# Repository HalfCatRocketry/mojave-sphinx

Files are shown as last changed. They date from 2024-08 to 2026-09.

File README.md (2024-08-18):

Mojave Sphinx is a high-power amateur rocket with a liquid bipropellant propulsion system powered by nitrous oxide and any number of solvent or hydrocarbon fuels. It is designed to be as simple and economical as possible so that an individual or team with high-power or experimental rocketry experience can build and launch it within a reasonable timeline and budget. Half Cat Rocketry provides the following:
- Build, Integration and Launch Guidebook - HCR-5100 (PDF)
- SolidWorks CAD files (.sldprt)
- SolidWorks drawing files (.slddrw)
- Drawing package (PDF)
- 3D models of machined, printed, and flat-cut components (.step and .stl)
- Vector files of flat-cut components (.dxf)
- HalfCatSim v1.3.8 motor simulation (.xlsx)
- Sample thrust curve file (.eng)
- OpenRocket simulation file (.ork)

Please note that the SolidWorks CAD was created in the version 2022 student edition and is for educational purposes.

Half Cat Rocketry is not liable for the usage of this content, and the authors bear no responsibility for the usage of its content. Read the following disclaimer before continuing.

DISCLAIMER:

By viewing, downloading, printing, or otherwise possessing the content in this repository you agree to the terms and conditions of its use, which are provided below. If you do not agree to the terms and conditions, you are required to remove this content from your possession by deleting all digital copies and/or disposing of printed materials in an environmentally responsible manner. Failure to do so shall constitute a violation of the license under which this content is distributed.

This content is provided as is, with absolutely NO WARRANTY, express or implied, including no warranty of merchantability or fitness for any particular purpose. You (“the user”) agree by your continued viewing or possession of this content to hold harmless and release from all liability the authors and any associated parties for any outcome resulting from your use or misuse of this material. The authors bear no responsibility for the usage of the this content, and any and all liability for injury, property damage, financial loss, death, or other harm arising from its use or misuse rests solely with the user.

This content is provided solely for informational and entertainment purposes and does not constitute an endorsement of, nor a recommendation to engage in, any particular activity, method, or practice. The information contained in this content solely represents the personal experiences of the authors and does not promise, guarantee, or predict any specific outcome of any particular activity, method, or practice.

The user acknowledges by continued viewing or possession of this content that rocketry and all associated activities, including but not limited to the procurement, manufacture, assembly, disassembly, modification, storage, handling, transport, operation, testing, launching, recovery and disposal of rocket and rocket motor systems, components, propellants, and accessories are inherently dangerous and may pose a direct and immediate hazard to health, life, and property.

Mentions of any particular products within this content by part number, name, description, brand, chemical formula, or any other identifier DO NOT constitute an endorsement of said products, nor is any warranty of merchantability or fitness for any particular purpose of said products expressed or implied by the authors of this content. Should the user purchase any product mentioned, listed, or otherwise discussed in this content, the user is solely responsible for determining the suitability of any and all products for the user’s specific application. The user is solely responsible for any outcome or liability arising from the use or misuse of any products named, described, or otherwise alluded to in this content.

As stated above, your (“the user’s”) continued viewing or possession of the content in this repository constitutes acknowledgement of and agreement to these warnings, terms, and conditions. If you do not agree to these terms and conditions, or do not wish to acknowledge the warnings provided herein, you are required to remove this content from your possession by deleting all digital copies and/or disposing of printed materials in an environmentally responsible manner. Failure to do so shall constitute a violation of the license under which this content is distributed.

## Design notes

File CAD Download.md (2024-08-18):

[Mojave Sphinx CAD Download](//drive.google.com/uc?export=download&id=1ExKPyPkNKFJ8Lf6YcyjYc9QDEeFzdeIZ) (Google Drive download link)

Please note that the zip file is large. (~250 MB)

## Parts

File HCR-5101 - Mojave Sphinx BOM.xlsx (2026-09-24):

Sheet: Cover Page
HCR-5101 | Mojave Sphinx Bill of Materials
Revision | 01 | This Bill of Materials (BOM) is a companion document to HCR-5100, the Mojave Sphinx Build, Integration, and Launch Guidebook. It is intended to be an easier format for referencing the book's BOM and purchasing parts. This document, HCR-5101, is considered the source of truth for the guidebook's BOM. It is separately controlled and released, allowing Half Cat Rocketry to make corrections or updates as necessary without needing to generate a revision of HCR-5100. A note on Revision 01: To avoid confusion between the guidebook's BOM (which does not reference this separate document, as it did not exist at the time of publication) and the BOM presented here, all descriptions and prices have been left as-shown in HCR-5100 R01, with only minor corrections to fix typos or broken links. More comprehensive updates will be introduced in the next revision, which will coincide with the release of HCR-5100 R02. A note on Amazon links: Amazon is a large marketplace with many stores and listings that often change much faster than we can keep up with. Therefore, Amazon line items generically link to the main website rather than a specific item's page. It is intended for the purchaser to search using the provided vendor description and part number then select appropriate items.
Release Date | 2026-04-25
Associated With | HCR-5100 (R01)
Revision | Release Date
01 | 2026-04-25

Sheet: Mojave Sphinx
A1 | Propellant Tank
Line | Item | Unit Price | QTY | Cost | Context | PN | Vendor Description | Source | Line | Alternate Source #1 | Alternate Source #2
1 | 6061 Aluminum Round 4"D X 1/2"L | $14.95 | 2 | $29.90 | Tank Bulkheads | 1610T37-1610T134 | Multipurpose 6061 Aluminum 4" Diameter (1/2 in) | https://www.mcmaster.com/1610T37-1610T134/ | 1
2 | 6061 Aluminum Round 4"D X 3"L | $22.26 | 1 | $22.26 | Tank Piston | 1610T37-1610T33 | Multipurpose 6061 Aluminum 4" Diameter (3 in) | https://www.mcmaster.com/1610T37-1610T33/ | 2
3 | 6061 Aluminum Tube 4"D X 1/8"W X 36"L | $85.38 | 1 | $85.38 | Tank Casing | 9056K42-9056K423 | Multipurpose 6061 Aluminum Round Tube 1/8" Wall Thickness, 4" OD (3 ft) | https://www.mcmaster.com/9056K42-9056K423/ | 3
4 | 6061 Aluminum Tube 4"OD X 1/2"W X 3"L | $10.37 | 2 | $20.74 | Bolted Tank Rings | 7392T17-7392T173 | Multipurpose 6061 Aluminum Round Tube 1/4" Wall Thickness, 4" OD (3 in) | https://www.mcmaster.com/7392T17-7392T173/ | 4
5 | -238 Buna-N O-Rings (Pack of 50) | $16.14 | 1 | $16.14 | Tank/Piston Seals | 9452K226 | Oil-Resistant Buna-N O-Ring 1/8 Fractional Width, Dash Number 238 | https://www.mcmaster.com/9452K226/ | 5
6 | 5/16-24 X 1/2" Button Head Screw (Pack of 25) | $7.57 | 1 | $7.57 | Tank Bolts | 91255A378 | Button Head Hex Drive Screw Black-Oxide Alloy Steel, 5/16"-24 Thread, 1/2" Long | https://www.mcmaster.com/91255A378/ | 6
7 | 5/16-24 Offset Narrow Base Weld Nut (Pack of 25) | $9.21 | 1 | $9.21 | Tank Bolt Nuts | 94579A550 | Steel Offset-Barrel Narrow-Base Weld Nut 5/16"-24 Thread Size | https://www.mcmaster.com/94579A550/ | 7
8 | 1/4-20 X 7/8 Button Head Hex Drive Screws (Pack of 50) | $9.30 | 1 | $9.30 | Fwd Bulkhead Recovery Anchors, Fin Brackets, Airframe | 91306A279 | Button Head Hex Drive Screws Zinc-Plated Alloy Steel, 1/4"-20 Thread, 7/8" Long | https://www.mcmaster.com/91306A279/ | 8
9 | 1/4-20 Coupling Nut | $0.39 | 2 | $0.78 | Fwd Bulkhead Recovery Anchors | 90264A435 | Zinc-Plated Steel Coupling Nut Low-Strength, 1/4"-20 Thread Size | https://www.mcmaster.com/90264A435/ | 9
10 | Sealing Washers for 1/4" Screw, 0.5" OD (Pack of 10) | $7.49 | 1 | $7.49 | Fwd Bulkhead Recovery Anchors | 91367A952 | Chemical-Resistant Fluorosilicone Sealing Washer for 1/4" Screw Size,.230" ID,.5" OD,.052" to .072" Thick | https://www.mcmaster.com/91367A952/ | 10
11 | Ultra-Low-Profile Socket Head Screw Alloy Steel, 1/4"-20 Thread Size, 1/2" Long | $4.93 | 2 | $9.86 | Propellant Piston Extraction | 90357A013 | Ultra-Low-Profile Socket Head Screw Alloy Steel, 1/4"-20 Thread Size, 1/2" Long | https://www.mcmaster.com/90357A013/ | 11
12 | Spacer, for 5/16”, 5/8” OD x 1/2" Long | $4.31 | 1 | $4.31 | Bushing for Tank Drill Jig | 93320A215 | Polished Unthreaded Spacers 5/8" OD, 1/2" Long, for 5/16" Screw Size | https://www.mcmaster.com/93320A215/ | 12
13 | Propellant Tank Casing | $0.00 | 1 | $0.00 | Machined | TANK-36L-047V2X8X313C | - | Made from 9056K423 | 13
14 | Fuel Tank Bulkhead | $0.00 | 1 | $0.00 | Machined | BKHD-FL-O238-4NPT2X250C | - | Made from 1610T134 | 14
15 | Oxidizer Tank Bulkhead | $0.00 | 1 | $0.00 | Machined | BKHD-OX-O238–8NPT4NPT | - | Made from 1610T134 | 15
16 | Propellant Piston | $0.00 | 1 | $0.00 | Machined | PSTN-2XO238-250T20 | - | Made from 1610T33 | 16
17 | Interface Ring | $0.00 | 2 | $0.00 | Machined | INRG-200S-8X3125C8X250C | - | Made from 7392T173 | 17
18 | Nut Retaining Ring | $0.00 | 2 | $0.00 | Printed | NTRG-45C20D-200E | - | Made from printer filament | 18
19 | Propellant Tank Drill Jig | $0.00 | 1 | $0.00 | Printed | DRLJG-TANK-8X625OD-BSHNG | - | Made from printer filament | 19
 |  | Subtotal |  | $222.94
A2 | Fluid System
Line | Item | Unit Price | QTY | Cost | Context | PN | Vendor Description | Source | Line | Alternate Source #1 | Alternate Source #2
1 | Aluminum Pipe Nipple, 1/4NPT, 4"L | $5.09 | 2 | $10.18 | Tank outlets to valves | 44665K137 | Standard-Wall Aluminum Pipe Nipple Threaded on Both Ends, 1/4 NPT, 4" Long | https://www.mcmaster.com/44665K137/ | 1
2 | Brass High Pressure Elbow Fitting, M/F, 1/4NPT | $2.94 | 2 | $5.88 | Fuel valve outlet | 50785K43 | High-Pressure Brass Pipe Fitting 90 Degree Elbow Adapter, 1/4 NPT Female x Male | https://www.mcmaster.com/50785K43/ | 2
3 | High-Pressure Brass Straight Reducer, 1/4 x 1/8 NPT Male | $2.64 | 1 | $2.64 | Fuel valve outlet | 5485K31 | High-Pressure Brass Pipe Fitting Straight Reducer, 1/4 x 1/8 NPT Male | https://www.mcmaster.com/5485K31/ | 3
4 | High-Pressure Brass Elbow Connector, 1/8 NPT Female | $3.31 | 1 | $3.31 | Fuel valve outlet | 50785K35 | High-Pressure Brass Pipe Fitting 90 Degree Elbow Connector, 1/8 NPT Female | https://www.mcmaster.com/50785K35/ | 4
5 | 37 Degree Flared Adapter for 5/16" Tube OD, 1/8 Pipe Size | $5.38 | 1 | $5.38 | Fuel valve outlet | 50675K435 | 37 Degree Flared Fitting for Copper Tubing Straight Adapter for 5/16" Tube OD, 1/8 Pipe Size | https://www.mcmaster.com/50675K435/ | 5
6 | High-Pressure Braided Chemical Hose with Fittings Brass 1/2"-20 Thread Size Flare UNF Female, 3/8" OD - 42" | $30.36 | 1 | $30.36 | Fuel Line 42" Section | 4468K858 | High-Pressure Braided Chemical Hose with Fittings Brass 1/2"-20 Thread Size Flare UNF Female, 3/8" OD (42 in) | https://www.mcmaster.com/4468K812-4468K858/ | 6
7 | High-Pressure Braided Chemical Hose with Fittings Brass 1/2"-20 Thread Size Flare UNF Female, 3/8" OD - 14" | $19.32 | 1 | $19.32 | Fuel Line 14" Section | 4468K031 | High-Pressure Braided Chemical Hose with Fittings Brass 1/2"-20 Thread Size Flare UNF Female, 3/8" OD (14 in) | https://www.mcmaster.com/4468K812-4468K031/ | 7
8 | High-Pressure Braided Chemical Hose with Fittings Brass 9/16"-18 Thread Size Flare UNF Female, 7/16" OD – 12” | $27.61 | 1 | $27.61 | Ox Line | 4468K865 | High-Pressure Braided Chemical Hose with Fittings Brass 9/16"-18 Thread Size Flare UNF Female, 7/16" OD (12 in) | https://www.mcmaster.com/4468K813-4468K865/ | 8
9 | 37 Degree Flared Straight Connector for 5/16" Tube OD, 1-3/8" Long | $4.47 | 1 | $4.47 | Fuel Line Union | 50675K135 | 37 Degree Flared Fitting for Copper Tubing Straight Connector for 5/16" Tube OD, 1-3/8" Long | https://www.mcmaster.com/50675K135/ | 9
10 | 37 Degree Flared Adapter for 3/8" Tube OD x 1/4 NPT Male | $3.65 | 1 | $3.65 | Ox Valve Outlet | 50675K163 | 37 Degree Flared Fitting for Copper Tubing Adapter for 3/8" Tube OD x 1/4 NPT Male | https://www.mcmaster.com/50675K163/ | 10
11 | Nylon Tubing, 1/4" OD, 800PSI, 10ft | $11.50 | 1 | $11.50 | Fill tube | 9685T3 | High-Pressure Hard Plastic Tubing for Air&Water Nylon, Semi-Clear White, 0.15" ID, 1/4" OD (10 ft) | https://www.mcmaster.com/9685T3/ | 11
12 | Check Valve, 1/8NPT Female/Male, Brass | $15.00 | 1 | $15.00 | Fill | 7768K21 | Brass Threaded Check Valve with Brass Piston, 1/8 NPT Female x NPT Male | https://www.mcmaster.com/7768K21/ | 12
13 | Elbow, 1/8NPT, Male/Female, Brass | $2.16 | 1 | $2.16 | Fill check to QD | 50785K41 | High-Pressure Brass Pipe Fitting 90 Degree Elbow Adapter, 1/8 NPT Female x Male | https://www.mcmaster.com/50785K41/ | 13
14 | Push to Connect Fitting, 1/4" Tube X 1/8NPT | $3.95 | 2 | $7.90 | Fill check to QD | 9396T31 | High-Pressure Push-to-Connect Tube Fitting for Air and Water, Adapter, 1/4" Tube OD x 1/8 NPTF Male | https://www.mcmaster.com/9396T31/ | 14
15 | 3/4" X 6" 6061-T6 Round Bar | $4.39 | 1 | $4.39 | QD Stock Material | 8974K299 | Multipurpose 6061 Aluminum 3/4" Diameter (1/2 ft) | https://www.mcmaster.com/8974K11-8974K299/ | 15
16 | -007 Buna-N O-rings (Pack of 100) | $4.25 | 1 | $4.25 | QD Seal | 9452K15 | Oil-Resistant Buna-N O-Ring 1/16 Fractional Width, Dash Number 007 | https://www.mcmaster.com/9452K15/ | 16
17 | High Pressure Brass Straight adapter, 1/4NPT Female x Male | $2.66 | 1 | $2.66 | Fuel valve outler spacer | 50785K27 | High-Pressure Brass Pipe Fitting Straight Adapter with Hex Body, 1/4 NPT Female x Male | https://www.mcmaster.com/50785K27/ | 17
18 | Quick Disconnect, ¾” x ⅛” Flange, 9/32” Female Bore, 1/8 NPT | $0.00 | 1 | $0.00 | Machined | QDC-750X125FLG-281FB8NPT |  | Made from 8974K299 | 18
19 | Quick Disconnect, ¾” x ⅛” Flange, .270 Male Barb, -007 O-Ring Gland | $0.00 | 1 | $0.00 | Machined | QDC-750x125FLG-270MB-O007 |  | Made from 8974K299 | 19
20 | Quick Disconnect Clip, for ¾” x ⅛” Flange | $0.00 | 1 | $0.00 | Printed | QDC-750X250CLP |  | Made from printer filament | 20
 |  | Subtotal |  | $160.66
A3 | Valves
Line | Item | Unit Price | QTY | Cost | Context | PN | Vendor Description | Source | Line | Alternate Source #1 | Alternate Source #2
1 | M3x0.5 10mm Low Profile Socket Head Screw, 18-8SS (Pack of 25) | $2.28 | 1 | $2.28 | Servo Horn Connector | DS3225 | 2Pack 25KG High Torque RC Servo Waterproof servo Compatible with 1/6, 1/8, 1/10, 1/12 RC Car, Full Metal Gear Steering Servo with 25T Servo Horn (270°) | https://www.amazon.com/ | 1
2 | 25kg Servo w/ 25T Servo Horn (Pack of 2) | $28.99 | 1 | $28.99 | Fuel/Ox valve actuators | 4112T22 | Compact High-Pressure Brass Ball Valve 2 | https://www.mcmaster.com/4112T22/ | 2
3 | Compact High Pressure Ball Valve, 1/4NPT | $17.26 | 2 | $34.52 | Fuel/Ox Valves | 90480A009 | Low-Strength Steel Hex Nut 1 | https://www.mcmaster.com/90480A009/ | 3
4 | 8-32 Hex Nut, Low Strength (Pack of 100) | $2.02 | 1 | $2.02 | Valve Handle Screw | 90591A141 | Zinc-Plated Steel Hex Nut 1 | https://www.mcmaster.com/90591A141/ | 4
5 | M4X0.7 Hex Nut, Low Strength (Pack of 100) | $1.90 | 1 | $1.90 | Servo mount screws | 90272A194 | Zinc-Plated Steel Pan Head Phillips Screw 1 | https://www.mcmaster.com/90272A194/ | 5
6 | 8-32 X 1/2"L Screw, Zinc Plated Steel (Pack of 100) | $3.98 | 1 | $3.98 | Valve Handle Screw | 91280A044 | Medium-Strength Class 8.8 Steel Hex Head Screw 1 | https://www.mcmaster.com/91280A044/ | 6
7 | M4X0.7 X 16mm Hex Head Screws, 18-8SS (Pack of 100) | $10.56 | 1 | $10.56 | Servo mount screws, Avbay Sled | 98689A113 | General Purpose 18-8 Stainless Steel Washer 1 | https://www.mcmaster.com/98689A113/ | 7
8 | M4 Washer, 8mm OD, 18-8SS (Pack of 100) | $3.43 | 1 | $3.43 | Servo mount screws | 92148A160 | 18-8 Stainless Steel Split Lock Washer 1 | https://www.mcmaster.com/92148A160/ | 8
9 | M4 Split Lock Washer, 18-8SS (Pack of 100) | $1.94 | 1 | $1.94 | Servo mount screws | 93475A210 | 18-8 Stainless Steel Washer | https://www.mcmaster.com/93475A210/ | 9
10 | M3 Flat Washer, 18-8SS, 7mm OD (Pack of 100) | $2.19 | 1 | $2.19 | Servo Horn Connector | 92855A310 | 18-8 Stainless Steel Low-Profile Socket Head Screws | https://www.mcmaster.com/92855A310/ | 10
11 | 3-pin Servo Extension Cables, 1m (Pack of 10) | $9.99 | 1 | $9.99 | Servo wires | SRV-3PIN-1MXT | 5 Pcs JR/Futaba Style Servo 1 to 2 Y Harness Leads Splitter Cable Male to Female Extension Lead Wire for RC Models Airplane 7cm | https://www.amazon.com/ | 11
12 | 3-Pin Servo Y-Harness | $7.99 | 1 | $7.99 | Optional; can make by splcing extensions | SRV-Y-HRNS | 5 Pcs JR/Futaba Style Servo 1 to 2 Y Harness Leads Splitter Cable Male to Female Extension Lead Wire for RC Models Airplane 7cm | https://www.amazon.com/ | 12
13 | PLA+ 3D Printer Filament, White, 2kg (Or Equivalent) | $45.99 | 1 | $45.99 | Valve actuator housings (NOTE: <1kg required for Valves; Also used on Airframe) | N/A | OVERTURE PLA Plus (PLA+) Filament 1.75mm PLA Professional Toughness Enhanced PLA Roll, Cardboard Spool, Premium PLA 2kg(4.4lbs), Dimensional Accuracy Probability +/- 0.02mm (White 2-Pack) | https://www.amazon.com/ | 13
14 | Servo Valve Mount | $0.00 | 1 | $0.00 | Printed | SABV-MOUNT-V2 | - | Made from printer filament | 14
15 | Servo Valve Handle Connector | $0.00 | 1 | $0.00 | Printed | SABV-HCON-V2 | - | Made from printer filament | 15
 |  | Subtotal |  | $153.50
A4 | Thrust Chamber Assembly
Line | Item | Unit Price | QTY | Cost | Context | PN | Vendor Description | Source | Line | Alternate Source #1 | Alternate Source #2
1 | 6061 Aluminum Round 3"D X 6"L | $23.23 | 1 | $23.23 | Nozzle and injector stock | 61ARB3 | 6061 Aluminum Round Bar (Size: 3 in, Length: 6 in) | https://www.midweststeelsupply.com/store/6061aluminumroundbar | 1 | https://www.mcmaster.com/8974K82-1610T41/
2 | 6061 Aluminum Tube 3"D X 1/2"W X 6"L | $37.00 | 1 | $37.00 | Chamber Tube | 61ARDT3500 | 6061 Aluminum Round Bar (Size: 3 X 1/2 in, Length: 6 in) | https://www.midweststeelsupply.com/store/6061aluminumroundtube | 2 | https://www.mcmaster.com/9056K23-9056K235/
3 | 110 Copper Round Bar 1-1/2" Diameter 2" Long | $18.88 | 1 | $18.88 | Nozzle Throat Insert | CRB112 | 110 Copper Round Bar (Size: 1-1/2 in, Length: 2 in) | https://www.midweststeelsupply.com/store/110copperroundbar | 3 | https://www.mcmaster.com/9103K9-9103K93/
4 | 37 Degree Flared Adapter for 5/16" Tube OD, 1/8 Pipe Size | $5.38 | 1 | $5.38 | Fuel Inlet | 50675K435 | 37 Degree Flared Fitting for Copper Tubing Straight Adapter for 5/16" Tube OD, 1/8 Pipe Size | https://www.mcmaster.com/50675K435/ | 4
5 | 37 Degree Flared Adapter for 3/8" Tube OD x 3/8 NPT Male | $5.18 | 1 | $5.18 | Ox Inlet | 50675K164 | 37 Degree Flared Fitting for Copper Tubing Adapter for 3/8" Tube OD x 3/8 NPT Male | https://www.mcmaster.com/50675K164/ | 5
6 | -141 Silicone O-rings (Pack of 10) | $10.17 | 1 | $10.17 | Injector Seals | 9396K79 | High-Temperature High-Purity Silicone O-Ring 3/32 Fractional Width, Dash Number 141 | https://www.mcmaster.com/9396K79/ | 6
7 | Inverted External Retaining Ring for 2.5" OD | $1.18 | 1 | $1.18 | Injector Flange | 90213A101 | Inverted External Retaining Ring for 2-1/2" OD, Black-Phosphate 1060-1090 Spring Steel | https://www.mcmaster.com/90213A101/ | 7
8 | Graphite Pipe Gasket, Size 1 | $2.83 | 2 | $5.66 | Chamber/nozzle seal | 94095K114 | High-Temperature Graphite Gasket for ANSI Class 600, for Pipe Size 1, 1-5/16" ID | https://www.mcmaster.com/94095K114/ | 8
9 | Flange Plate, Thrust Chamber, Steel, 1/4" | $9.28 | 2 | $18.56 | Chamber flanges | FLNG-ST-25T-8X250C | - | https://sendcutsend.com/ | 9
10 | Bracket, Thrust Chamber Mounting, Aluminum, 1/8" | $5.18 | 8 | $41.44 | Chamber attachment to fin brackets | BRKT-90A-125T-2X250C | - | https://sendcutsend.com/ | 10
11 | 1/4 Washers 5/8" OD 18-8SS (Pack of 100) | $5.50 | 2 | $11.00 | Chamber tie rods, fins, avbay | 92141A029 | 18-8 Stainless Steel Washer for 1/4" Screw Size, 0.281" ID, 0.625" OD | https://www.mcmaster.com/92141A029/ | 11
12 | Split Lock Washer for 1/4 Screw Size (Pack of 100) | $3.02 | 1 | $3.02 | Chamber tie rods, fins, avbay | 91102A750 | Zinc-Plated Steel Split Lock Washer for 1/4" Screw Size, 0.26" ID, 0.487" OD | https://www.mcmaster.com/91102A750/ | 12
13 | 1/4-20 Medium Strength Hex Nuts (Pack of 100) | $7.08 | 1 | $7.08 | Chamber tie rods, fins, avbay | 95505A601 | Medium-Strength Steel Hex Nut Grade 5, 1/4"-20 Thread Size | https://www.mcmaster.com/95505A601/ | 13
14 | 1/4-20 x 8"L Black Oxide Threaded on Both Ends Stud | $2.59 | 8 | $20.72 | Chamber tie rods (NOTE: Add'l qty on Airframe) | 90281A102 | Black-Oxide Steel Threaded on Both Ends Stud 1/4"-20 Thread Size, 8" Long, 1" Long Threads | https://www.mcmaster.com/90281A102/ | 14
15 | Low-Profile Ultra-Wd Truss Head Slotted Screw 1/4"-20 Thread, 3/4" Long | $8.32 | 1 | $8.32 | Scrintle Screw | 90015A410 | Low-Profile Ultra-Wd Truss Head Slotted Screw 1/4"-20 Thread, 3/4" Long | https://www.mcmaster.com/90015A410/ | 15
16 | High-Temperature Dry-Running 841 Bronze Sleeve Bearing for 1/4" Shaft Diameter and 3/8" Housing ID, 3/8" Long | $0.97 | 1 | $0.97 | Scrintle Sleeve | 9368T14 | High-Temperature Dry-Running 841 Bronze Sleeve Bearing for 1/4" Shaft Diameter and 3/8" Housing ID, 3/8" Long | https://www.mcmaster.com/9368T14/ | 16
17 | Garter Spring Hard Drawn Steel, 1.529" OD, 1.341" ID | $5.31 | 1 | $5.31 | Nozzle Insert Retainer | 8284N57 | Garter Spring Hard Drawn Steel, 1.529" OD, 1.341" ID | https://www.mcmaster.com/8284N57/ | 17
18 | Injector, Basic Orifice Pattern | $0.00 | 1 | $0.00 | Machined | INJC-2X8NPT-38NPT-250T20-2XO230-BASIC | - | Made from 61ARB3 | 18
19 | Nozzle, for Throat Insert | $0.00 | 1 | $0.00 | Machined | NZZL-45C20D-200E | - | Made from 61ARB3 | 19
20 | Combustion Chamber | $0.00 | 1 | $0.00 | Machined | CMBR-200DI-250B-525L | - | Made from 61ARDT3500 | 20
21 | Throat Insert, Spring Retained | $0.00 | 1 | $0.00 | Machined | THRT-45C20D-100T |  | Made from CRB112 | 21
 |  | Subtotal |  | $223.10
A5 | Igniter
Line | Item | Unit Price | QTY | Cost | Context | PN | Vendor Description | Source | Line | Alternate Source #1 | Alternate Source #2
1 | Thick-Wall Pipe Nipple, 1/2NPT X 2"L, Aluminum | $8.28 | 1 | $8.28 | Cartridge body | 2155K18 | Thick-Wall Aluminum Pipe Nipple https://www.mcmaster.com/50785K164/ | https://www.mcmaster.com/2155K18/ | 1
2 | 1/2NPT Cap, Brass | $2.96 | 1 | $2.96 | Cartridge cap | 50785K164 | High-Pressure Brass Pipe Fitting https://www.mcmaster.com/4429K421/ | https://www.mcmaster.com/50785K164/ | 2
3 | 1/2NPT Coupling, Brass | $4.05 | 1 | $4.05 | Cartridge body | 50785K94 | High-Pressure Brass Pipe Fitting https://www.mcmaster.com/50785K25/ | https://www.mcmaster.com/50785K94/ | 3
4 | NPT Bushing, 1/2 Male X 1/8 Female, Brass | $4.72 | 1 | $4.72 | Cartridge bottom | 4429K421 | Low-Pressure Brass Threaded Pipe Fitting https://www.mcmaster.com/50785K91/ | https://www.mcmaster.com/4429K421/ | 4
5 | Pipe Nipple, 1/8NPT X 2"L, Brass | $2.78 | 1 | $2.78 | Cartridge outlet | 50785K171 | High-Pressure Brass Pipe Fitting 0 | https://www.mcmaster.com/50785K171/ | 5
6 | High-Pressure Brass Pipe Fitting Straight Adapter with Hex Body, 1/8 NPT Female x Male | $1.40 | 1 | $1.40 | Cartridge outlet | 50785K25 | High-Pressure Brass Pipe Fitting 0 | https://www.mcmaster.com/50785K25/ | 6
7 | High-Pressure Brass Pipe Straight Connector, 1/8 NPT Male | $1.60 | 1 | $1.60 | Cartridge outlet | 5485K21 | High-Pressure Brass Pipe Fitting 0 | https://www.mcmaster.com/5485K21/ | 7
8 | High-Pressure Brass Straight Connector with Hex Body, 1/8 NPT Female | $1.46 | 1 | $1.46 | Igniter inlet | 50785K91 | High-Pressure Brass Pipe Fitting 0 | https://www.mcmaster.com/50785K91/ | 8
 |  | Subtotal |  | $27.25
A6 | Airframe
Line | Item | Unit Price | QTY | Cost | Context | PN | Vendor Description | Source | Line | Alternate Source #1 | Alternate Source #2
1 | Nose Cone Shoulder, 4X 1/4" Rod Sleeves, for 8X 8-32 Hex Nuts with Clearance Holes | $0.00 | 1 | $0.00 | 3D Printed from filament on Valves BOM | NSCN-SLDR-4X250R8X832HNC | - | Printed | 1
2 | Nose Cone, Section 1, 4X 1/4" Rod Sleeves | $0.00 | 1 | $0.00 | 3D Printed from filament on Valves BOM | NSCN-SC1-4X250R | - | Printed | 2
3 | Nose Cone, Section 2, 4X 1/4" Rod Sleeves | $0.00 | 1 | $0.00 | 3D Printed from filament on Valves BOM | NSCN-SC2-4X250R | - | Printed | 3
4 | Nose Cone, Tip, 4X 1/4" Rod Sleeves, 1/4" Clearance Hole with Hex Nut Capture | $0.00 | 1 | $0.00 | 3D Printed from filament on Valves BOM | NSCN-TIP-4X250R250HNC | - | Printed | 4
5 | 1/4-20 Nylon Threaded Rod, 24"L | $6.35 | 2 | $12.70 | Nose Cone Tension Rods | 98831A028 | Nylon Threaded Rod 1/4"-20 Thread Size, 2 Feet Long (White) | https://www.mcmaster.com/98831A360-98831A028/ | 5
6 | Cadmium-Plated Steel MIL. Spec. Washer for 1/4" Screw Size, NAS 1149-F0432P | $5.21 | 1 | $5.21 | Nose Cone Tension Rods | 95229A420 | Cadmium-Plated Steel MIL. Spec. Washer for 1/4" Screw Size, NAS 1149-F0432P | https://www.mcmaster.com/95229A420/ | 6
7 | Galvanized Steel Eyebolt with Nut and with Shoulder, for Lifting, 1/4"-20 Thread Size, 1-1/2" Thread Length, 3" Shank | $5.54 | 1 | $5.54 | Nose Cone Recovery Anchor | 3018T23 | Galvanized Steel Eyebolt with Nut and with Shoulder for Lifting, 1/4"-20 Thread Size, 1-1/2" Thread Length, 3" Shank | https://www.mcmaster.com/3018T23/ | 7
8 | 316 Stainless Steel Cap Nut, 1/4"-20 Thread Size | $2.99 | 1 | $2.99 | Nose Cone Eyebolt Nut | 92994A029 | 316 Stainless Steel Cap Nut Super-Corrosion-Resistant, 1/4"-20 Thread Size | https://www.mcmaster.com/92994A029/ | 8
9 | Airframe - 4" Mailing Tube, 36"L | $8.60 | 1 | $8.60 | .08" Wall Cardboard, White | 20545T38 | Round Shipping Tube with Press-on End Caps, 4" ID, 36" Inside Length | https://www.mcmaster.com/20545T38/ | 9
10 | Avionics Bay Coupler, Half, 3.994” OD, Printed | $0.00 | 1 | $0.00 | 3D Printed from filament on Valves BOM | AVBY-HF-3994 | - | Printed | 10
11 | Avionics Bay Switch Band, 4.16” OD, Printed | $0.00 | 1 | $0.00 | 3D Printed from filament on Valves BOM | AVBY-SB-4160 | - | Printed | 11
12 | 1/4-20 x 8"L Black Oxide Threaded on Both Ends Stud | $2.59 | 6 | $15.54 | Coupler tension rods, Recovery Bulkhead Studs (Note: Add'l QTY on Chamber) | 90281A102 | Black-Oxide Steel Threaded on Both Ends Stud 1/4"-20 Thread Size, 8" Long, 1" Long Threads | https://www.mcmaster.com/90281A102/ | 12
13 | U-Bolt with Mounting Plate, Galvanized, 1/4"-20 Thread Size, 1" ID | $1.31 | 3 | $3.93 | Shock Cord Anchor Point | 3043T643 | U-Bolt with Mounting Plate, Zinc-Plated Steel, 1/4"-20 Thread Size, 1" ID | https://www.mcmaster.com/3043T643/ | 13
14 | 1/4-20 X 10"L Threaded Rod, B7 Medium Strength | $3.60 | 2 | $7.20 | Avbay rods | 92580A328 | Grade B7 Medium-Strength Steel Threaded Rod 1/4"-20 Thread Size, 10" Long | https://www.mcmaster.com/92580A328/ | 14
15 | Aluminum Angle, 1" X 1" X 1/8" X 24"L | $7.59 | 4 | $30.36 | Fin brackets | 89822K402 | Multipurpose 6061 Aluminum 90 Degree Angle with Round Edge, 1/8" Thickness, 1" High x 1" Wide Outside | https://www.mcmaster.com/8982K4-8982K402/ | 15
16 | Spacer, Fin Bracket to Tank | $0.00 | 4 | $0.00 | 3D Printed from filament on Valves BOM | SPCR-400SD-250C0313C | - | Printed | 16
17 | 1/4" x 12" x 24" Birch Plywood | $18.48 | 1 | $18.48 | Fins | 1125T412 | Marine-Grade Plywood Sheet 12" x 24" x 1/4" | https://www.mcmaster.com/1125T412/ | 17
18 | 5/16-24 X 7/8" Button Head Screws (Pack of 10) | $4.17 | 1 | $4.17 | Fin Bracket Attachment to Tank | 91255A839 | Button Head Hex Drive Screw Black-Oxide Alloy Steel, 5/16"-24 Thread, 7/8" Long | https://www.mcmaster.com/91255A839/ | 18
19 | Aluminum Foil Tape, Acrylic Adhesive, 2" Wide, 15 Feet Length, 0.005" Thick | $7.79 | 1 | $7.79 | Coupler Shimming | 7631A82 | Foil HVAC Tape Acrylic Adhesive, 2" Wide, 15 Feet Length, 0.005" Overall Thickness | https://www.mcmaster.com/7631A82/ | 19
20 | 18-8 Stainless Steel Flanged Button Head Screw, 1/4"-20 Thread, 1-1/4" Long (Pack of 5) | $6.44 | 1 | $6.44 | Rail Button Screws | 97654A620 | 18-8 Stainless Steel Flanged Button Head Screw 1/4"-20 Thread, 1-1/4" Long | https://www.mcmaster.com/97654A620/ | 20
21 | Rail Button, 1515, Printed, Part A | $0.00 | 2 | $0.00 | 3D Printed from filament on Valves BOM | RLBTN-A-1515-250C | - | Made from printer filament | 21
22 | Rail Button, 1515, Printed, Part B | $0.00 | 2 | $0.00 | 3D Printed from filament on Valves BOM | RLBTN-B-1515-250C | - | Made from printer filament | 22
23 | Lower Airframe Template | $0.00 | 1 | $0.00 | Printed | TMPLT-AF-LWR-416 | - | Made from printer filament | 23
24 | Upper Airframe Template | $0.00 | 1 | $0.00 | Printed | TMPLT-AF-UPR-416 | - | Made from printer filament | 24
25 | Upper Airframe Backing Plug | $0.00 | 1 | $0.00 | Printed | PLG-DRIL-AF-UPR-416 | - | Made from printer filament | 25
26 | Fin Bracket Template, Aft | $0.00 | 1 | $0.00 | Printed | TMPLT-FIN-BRKT-1X1-AFT | - | Made from printer filament | 26
27 | Fin Bracket Template, Forward | $0.00 | 1 | $0.00 | Printed | TMPLT-FIN-BRKT-1X1-FWD | - | Made from printer filament | 27
 |  | Subtotal |  | $128.95
A7 | Recovery
Line | Item | Unit Price | QTY | Cost | Context | PN | Vendor Description | Source | Line | Alternate Source #1 | Alternate Source #2
1 | Eggtimer Quark Dual Deploy Altimeter Kit | $20.00 | 2 | $40.00 | Deployment controller | EGTMR-QRK | Eggtimer Quark Deployment Controller | http://eggtimerrocketry.com/home/altimeters-av-bay/ | 1 | https://www.perfectflitedirect.com/stratologgercf-altimeter/ | https://www.missileworks.com/rrc3
2 | 7.2ft Hexagonal Tent Tarp, Main Chute Canopy | $24.99 | 1 | $24.99 | Alternate main chute canopy (saves $55.94) | CNPY-CHT-86IN | Hikeman Hexagonal Tent Footprint,1-4 Person Ultralight Waterproof Tent Tarp Ground Sheet Mat with 6 Tent Stakes for Camping Hiking Picnic Backpacking (Medium) | https://www.amazon.com/ | 2
3 | 250lb Kevlar Cord, 100ft | $13.95 | 1 | $13.95 | Main chute canopy shroud lines | CRD-KVLR-250LB | emma kites 100% Kevlar Braided String Utility Cord Abrasion Flame Resistant, Tactical Survival Fishing Assist Cord Model Rocket Paracord Trip Line Camping Cordage | https://www.amazon.com/ | 3
4 | Drogue Parachute, 36” Diameter | $20.00 | 1 | $20.00 | Drogue chute | REC-CHT-DRG-36 | 36in Topflight Chute | https://www.csrocketry.com/recovery-supplies/top-flight-recovery/standard-parachutes/36in-topflight-chute.html | 4 | http://www.topflightrecoveryllc.com/page1.html
5 | Tubular Nylon Shock Cord, 3000lbf Breaking Strength | $0.55 | 50 | $27.50 | Shock cord | REC-TNSC-3KLB | 5/8" Yellow Tubular Nylon (50 ft) | https://www.csrocketry.com/recovery-supplies/hardware-and-shock-chord/kevlar-and-nylon-shock-chord/5/8-yellow-tubular-nylon.html | 5 | https://www.strapworks.com/58-inch-blue-water-tubular-hot-orange
6 | Parachute Protector, Nomex, 16 X 16” | $9.50 | 2 | $19.00 | Main and Drogue Chute Protector | REC-PRT-16 | 16" SkyAngle Chute Protector | https://www.csrocketry.com/recovery-supplies/skyangle/protectors/16-skyangle-chute-protector.html | 6 | http://www.topflightrecoveryllc.com/page3.html
7 | Avionics Bay Sled, Plywood, 2.25” X 6.00”, 6X M4 Clearance Holes | $0.00 | 1 | $0.00 | Avbay sled | AVBY-SLD-225X600- 6XM4C | - | Made from printer filament + plywood | 7
8 | Bulkhead, Recovery/Avionics Bay, 3.99” OD, 4X 1/4" Clearance Holes | $6.78 | 3 | $20.34 | Avbay bulkheads, recovery bulkhead | BKHD-REC-399-250C-2X170WE | - | https://sendcutsend.com/ | 8
9 | Avionics Bay Bulkhead Centering Ring, for 4-Rod Coupler | $0.00 | 2 | $0.00 | Avbay centering rings | AVBY-CR-4R | - | Made from printer filament | 9
10 | Avionics Bay Sled Mount, for .25” Rods, M4 Clearance Holes | $0.00 | 1 | $0.00 | Avbay sled mount | AVBY-MT-250R-M4C | - | Made from printer filament | 10
11 | Avionics Bay Battery Holder, 2X 9V Batteries, for .25” Rods, M4 Clearance Holes | $0.00 | 1 | $0.00 | Avbay battery holder | AVBY-BH-2X9V250R-M4C | - | Made from printer filament | 11
12 | Hex Standoffs, 2-56, Aluminum | $0.52 | 4 | $2.08 | Altimeter mounting | 93505A211 | Male-Female Threaded Hex Standoff Aluminum, 3/16" Hex Size, 1/4" Long, 2-56 Thread Size | https://www.mcmaster.com/93505A211/ | 12
13 | Nylon Washers, #2 Screw Size | $3.97 | 1 | $3.97 | Altimeter Insulation | 91755A200 | Self-Retaining Washer for # 2 & M2 Size, 0.115" ID, 0.203" OD, 0.022"-0.042" Thick | https://www.mcmaster.com/91755A152-91755A200/ | 13
14 | Nylon Pan Head Screws, Phillips, 2-56 Thread, 1/4" Long | $8.43 | 1 | $8.43 | Altimeter mounting, Shear Pins, Nose Cone | 94735A707 | Nylon Pan Head Screws Phillips, 2-56 Thread, 1/4" Long | https://www.mcmaster.com/93135A013/ | 14
15 | 9V Battery Connector | $1.21 | 2 | $2.42 | Altimeter Power | 7712K511 | Battery Holder 1 9V Battery, T-Shape with Single Layout, 1.04" Long | https://www.mcmaster.com/7712K511/ | 15
16 | 9V Alkaline Batteries (Pack of 2) | $8.00 | 1 | $8.00 | Altimeter Power | 9V-BATT | 9 Volt Battery | Retail Store | 16
17 | Quick Link 1400lb Capacity | $2.97 | 4 | $11.88 | Shock cord attachment | 8947T26 | Oval-Shaped Threaded Connecting Link Type 316 Stainless Steel, 1/4" Thickness, 5/16" Opening, Not for Lifting | https://www.mcmaster.com/8947T26/ | 17
18 | 20GA Silicone Coated Wire, Red & Black, 10ft Each | $8.99 | 1 | $8.99 | Avbay wiring | 20GA-RBP | 20 Gauge Wire 20 feet Silicone Wire Soft and Flexible Tinned Copper Wire High Temperature Resistance 10 ft Black and 10 ft Red Stranded Wire for 3D Printer, Test Leads, RC Applications | https://www.amazon.com/ | 18
 |  | Subtotal |  | $211.55
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

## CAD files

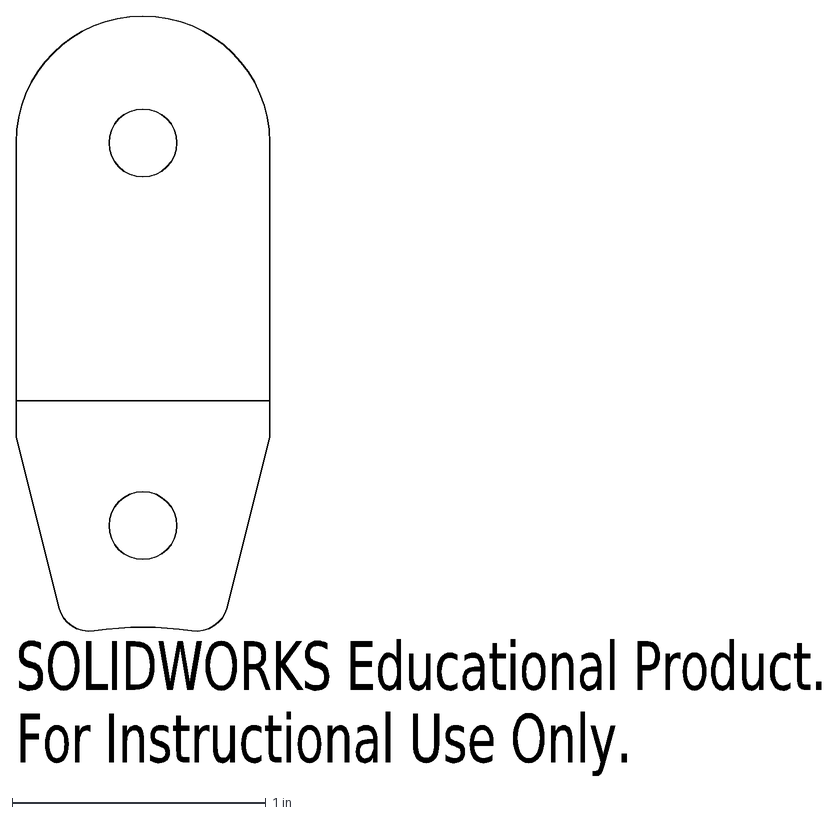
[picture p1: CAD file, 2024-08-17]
Flat-Cut Components/DXF/Flat pattern - BRKT-90A-125T-2X250C Bracket, Thrust Chamber Mounting, Mojave Sphinx.DXF
SOLIDWORKS Educational Product.
For Instructional Use Only.

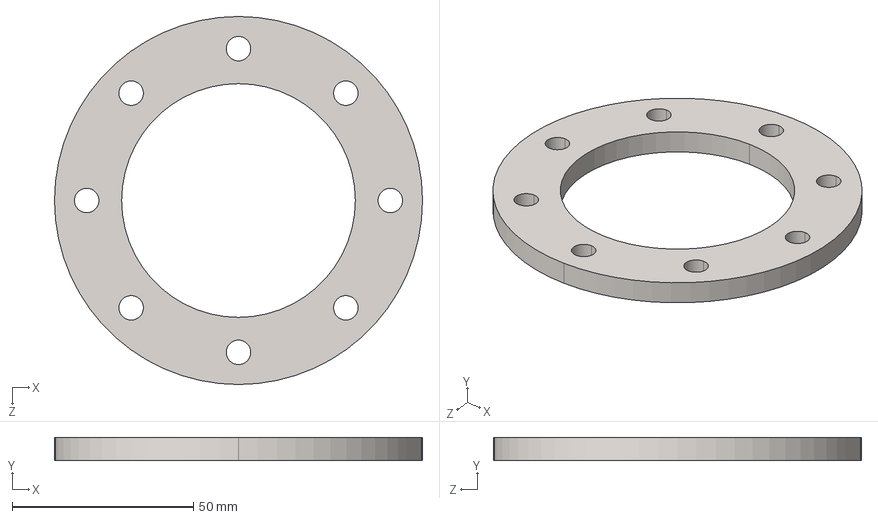
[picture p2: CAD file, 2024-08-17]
Flat-Cut Components/STEP/FLNG-ST-25T-8X250C Flange Plate, Thrust Chamber, Mojave Sphinx.STEP
101.6 x 6.35 x 101.6 mm

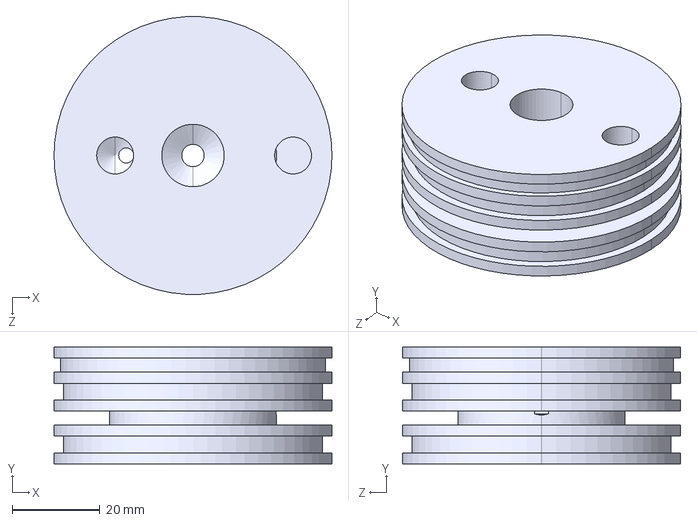
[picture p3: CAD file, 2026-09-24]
Machined Components/STEP/INJC-2X8NPT-38NPT-250T20-2XO230-BLANK Injector, Blank, Mojave Sphinx.STEP
63.5 x 26.7 x 63.4 mm

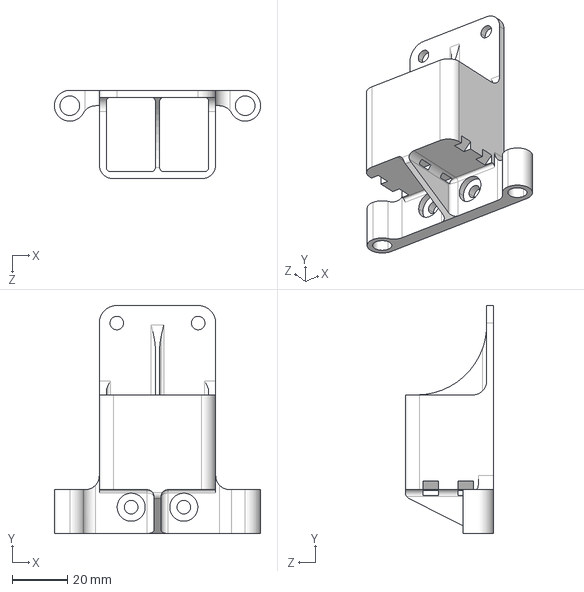
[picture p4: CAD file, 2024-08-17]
Printed Components/STEP/AVBY-BH-2X9V-250R-M4C Battery Holder, Avbay, Mojave Sphinx.STEP
74.7 x 82.5 x 32.0 mm

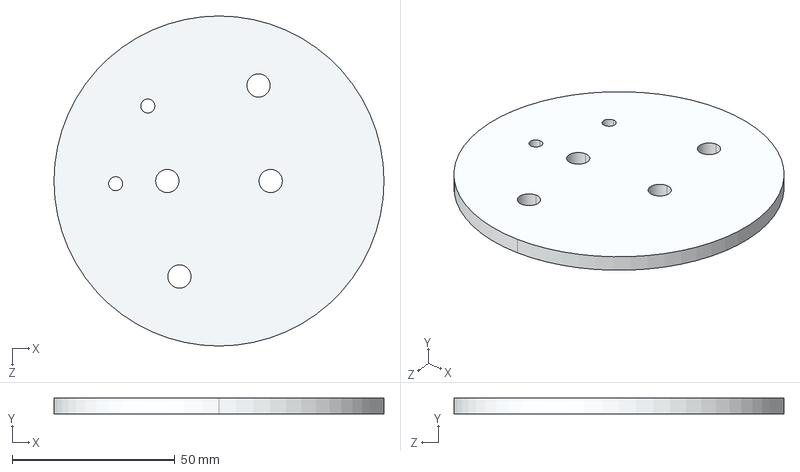
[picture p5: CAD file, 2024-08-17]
Flat-Cut Components/STEP/BKHD-REC-4X250C-2X170WE Bulkhead, Recovery and Avionics Bay, Mojave Sphinx.STEP
101.3 x 4.78 x 101.3 mm

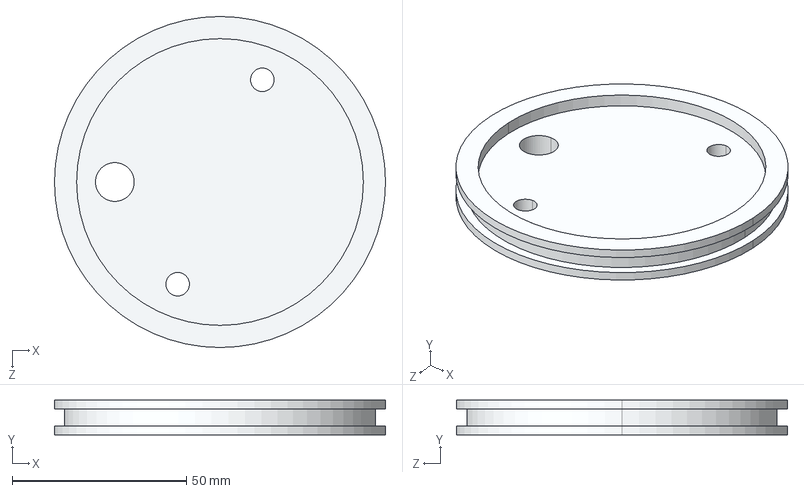
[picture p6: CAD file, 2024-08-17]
Machined Components/STEP/BKHD-FL-O238-4NPT-2X250C Tank Bulkhead, Fuel, Mojave Sphinx.STEP
95.0 x 9.91 x 95.0 mm

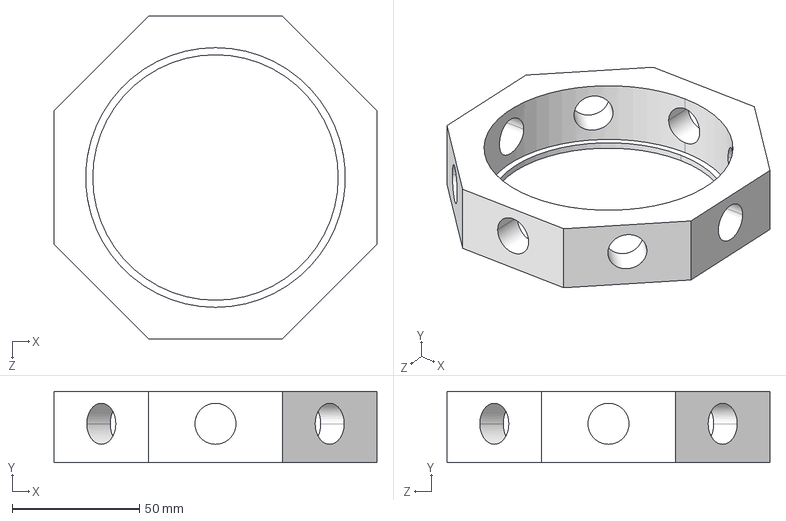
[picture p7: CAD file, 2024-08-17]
Printed Components/STEP/DRLJG-TANK-8X625OD-BSHNG.STEP
127.0 x 27.9 x 127.0 mm

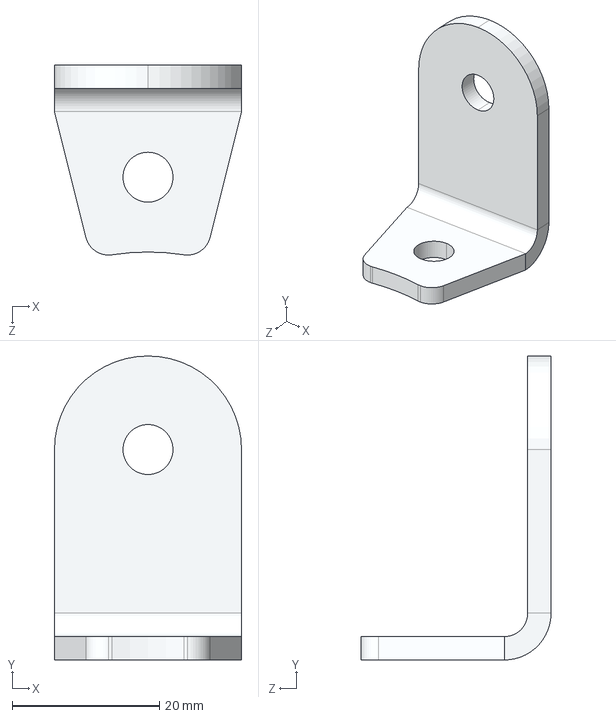
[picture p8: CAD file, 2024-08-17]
Flat-Cut Components/STEP/BRKT-90A-125T-2X250C Bracket, Thrust Chamber Mounting, Mojave Sphinx.STEP
25.4 x 41.3 x 25.8 mm

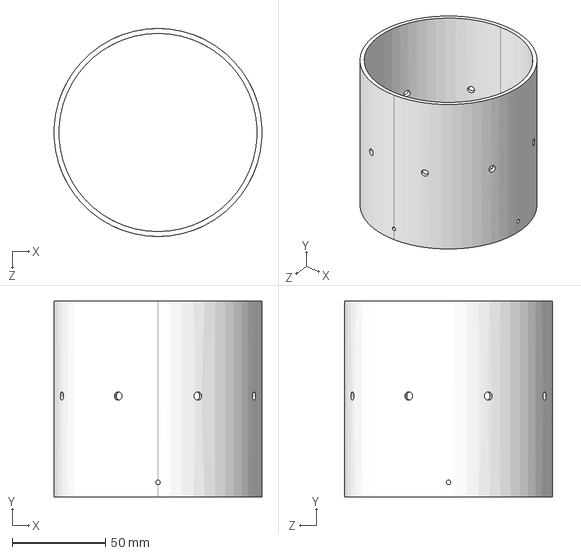
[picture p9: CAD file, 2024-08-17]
Printed Components/STEP/TMPLT-AF-UPR-416 Template, Hole Marking, Upper Airframe Tube, Mojave Sphinx.STEP
111.3 x 104.8 x 111.3 mm

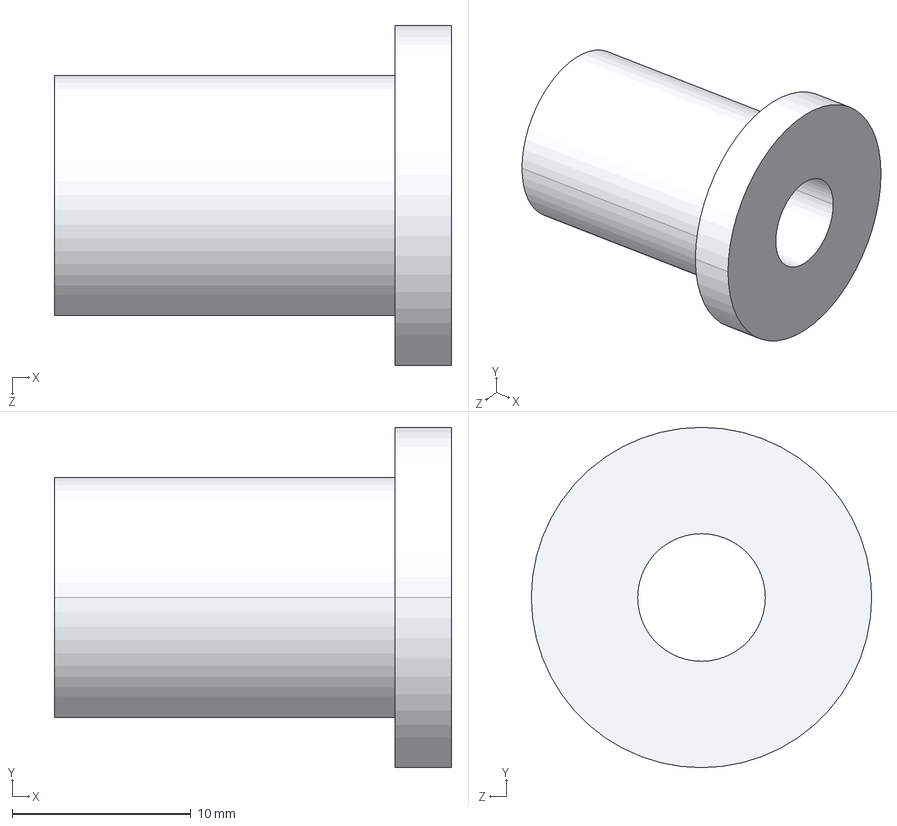
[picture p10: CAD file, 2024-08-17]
Machined Components/STEP/QDC-750X125FLG-281FB-8NPT Quick Disconnect, Female, Mojave Sphinx.STEP
22.2 x 19.1 x 19.1 mm

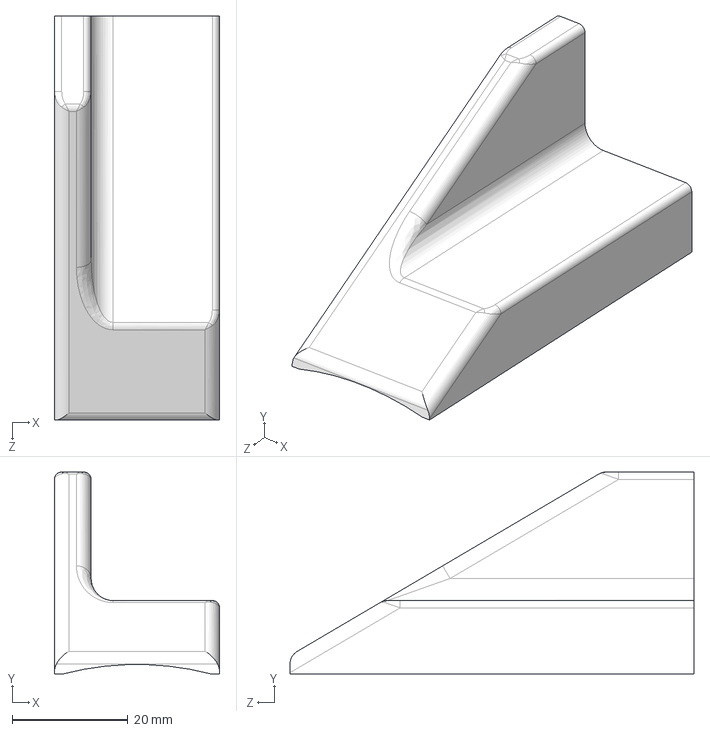
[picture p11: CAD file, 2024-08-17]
Printed Components/STEP/AERO-100X100X0125 Aerodynamic Fin Bracket Tip, for 1.00 X 1.00 X .125 Aluminum Angle, Mojave Sphinx.STEP
28.6 x 34.9 x 69.8 mm

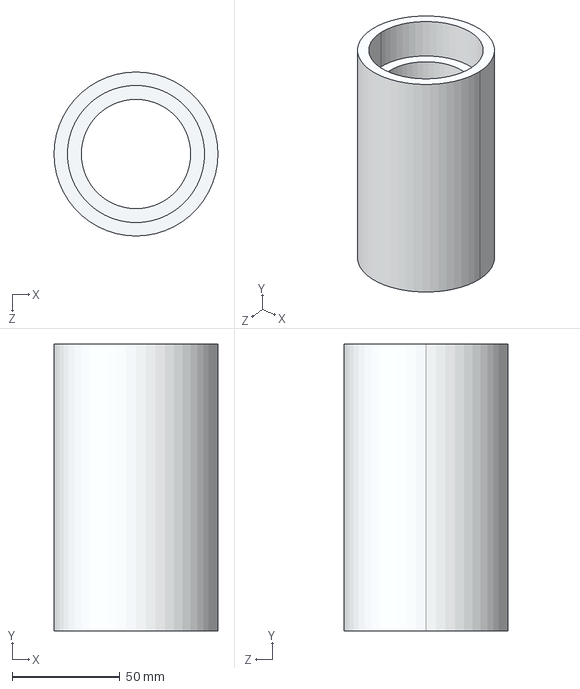
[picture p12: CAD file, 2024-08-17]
Machined Components/STEP/CMBR-200DI-250B-525L Combustion Chamber, Mojave Sphinx.STEP
76.2 x 133.3 x 76.2 mm

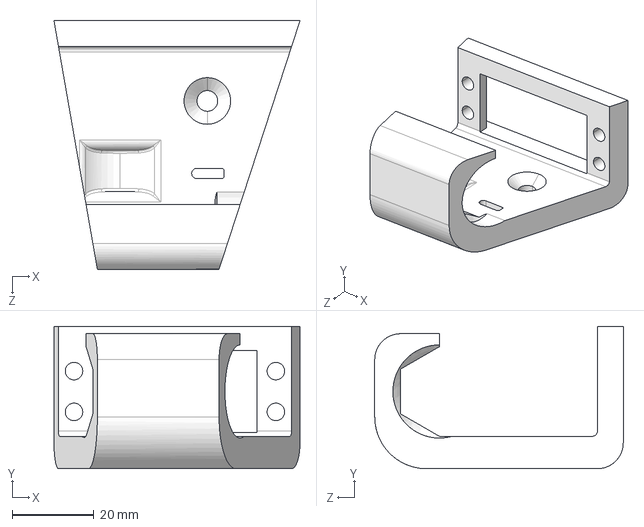
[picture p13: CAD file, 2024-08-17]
Printed Components/STEP/SABV-MNT-04V-3225S Mount, Servo Actuated Ball Valve, Hex Clearance, Mojave Sphinx.STEP
60.3 x 34.9 x 60.9 mm

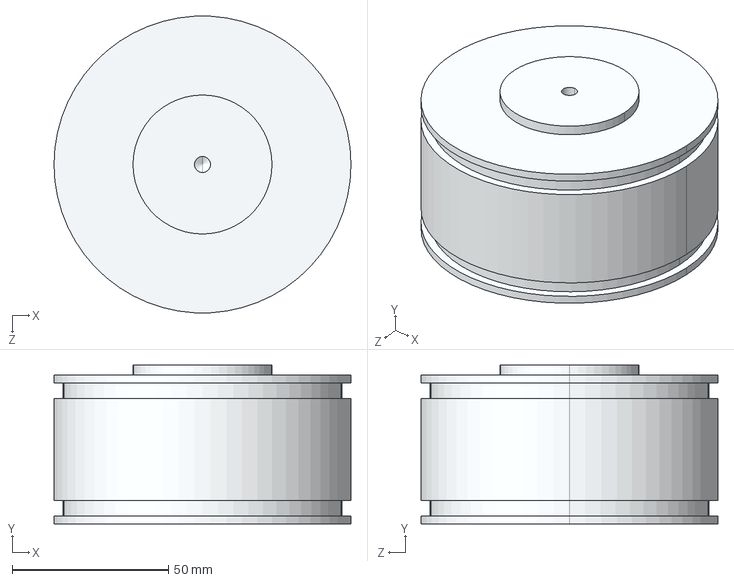
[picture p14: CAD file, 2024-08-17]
Machined Components/STEP/PSTN-2XO238-250T20 Propellant Piston, Mojave Sphinx.STEP
95.0 x 50.8 x 94.9 mm

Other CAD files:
Machined Components/STEP/BKHD-OX-O238-8NPT-4NPT Tank Bulkhead, Oxidizer, Mojave Sphinx.STEP
Machined Components/STEP/THRT-45C20D-100T Throat Insert, Spring Retained, Mojave Sphinx.STEP
Printed Components/STEP/PLG-DRL-AF-UPR1-416 Backing Plug, Sacrificial, for Upper Airframe Tube Drilling.STEP
Machined Components/STEP/NZZL-45C20D-200E Nozzle, for Throat Insert, Mojave Sphinx.STEP
Flat-Cut Components/DXF/BKHD-REC-4X250C-2X170WE Bulkhead, Recovery and Avionics Bay, Mojave Sphinx.DXF
Flat-Cut Components/DXF/FLNG-ST-25T-8X250C Flange Plate, Thrust Chamber, Mojave Sphinx.DXF
Flat-Cut Components/STL/BKHD-REC-4X250C-2X170WE Bulkhead, Recovery and Avionics Bay, Mojave Sphinx.STL
Flat-Cut Components/STL/BRKT-90A-125T-2X250C Bracket, Thrust Chamber Mounting, Mojave Sphinx.STL
Flat-Cut Components/STL/FLNG-ST-25T-8X250C Flange Plate, Thrust Chamber, Mojave Sphinx.STL
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

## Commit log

2024-08-17 update folder names
    [AERO-100X100X0125 Aerodynamic Fin Bracket Tip, for 1.00 X 1.00 X .125 Aluminum Angle, Mojave Sphinx.STEP, AERO-100X100X0125 Aerodynamic Fin Bracket Tip, for 1.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]
2024-08-18 Create CAD Download.md
2024-08-18 Update CAD Download.md
